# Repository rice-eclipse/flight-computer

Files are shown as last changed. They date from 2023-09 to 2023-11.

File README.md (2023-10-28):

# Strix
Custom STM32-Based flight computer to gather data from IMUs, altimeters, and GPS, and control in-flight pyrotechnic events. The software running on this board was created in STM32CubeMX, and stored in a different repository.

This repository contains KiCAD schematics and layouts for this flight computer. The schematics use hierarchical schematic sheets, with sheets defined for the microcontroller, sensors/data storage, pyrotechnic channels, connectors, and power supply.

## Notes
Manufacturing exports go in the fabrication folder (ignored by .gitignore)

## Additional Documentation:
[docs/strix.md](docs/strix.md)

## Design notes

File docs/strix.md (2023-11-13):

# Strix

Strix is a completely student researched and designed flight computer. It was created to record data, transmit telemetry, and control in-flight events in Eclipse's rockets. It is intended to supplement/replace altimeters and flight computers Eclipse currently uses, including the Missileworks RRC2+, Featherweight Altimeters Raven Blue, and Altus Metrum TeleMega.

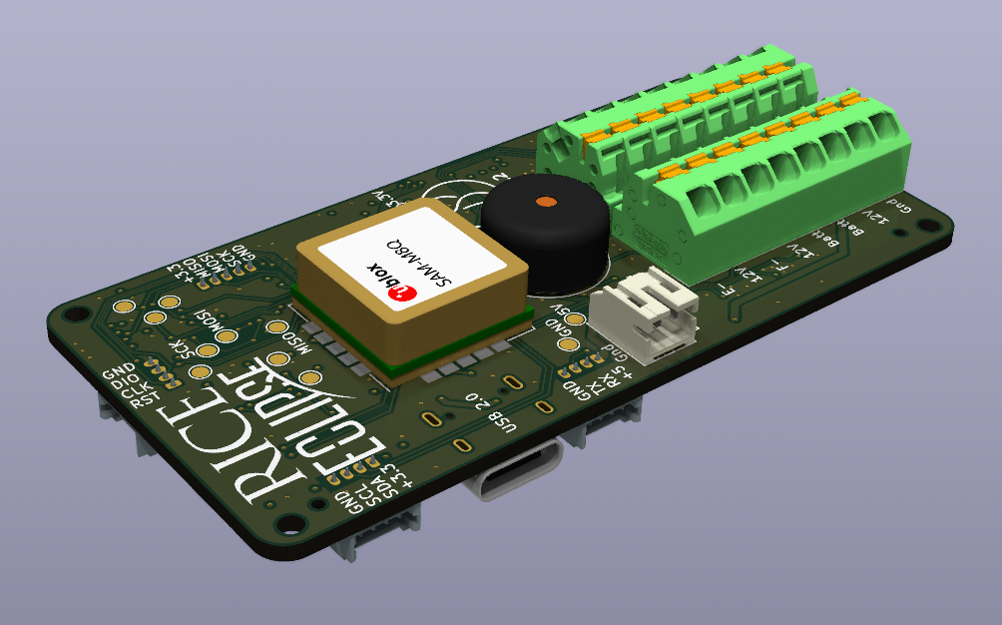
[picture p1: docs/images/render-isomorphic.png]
Isomorphic view of Strix


## Requirements

Strix was designed with several requirements in mind. It must:

1. Read linear and angular acceleration data from two different accelerometers
2. Read barometric altitude
3. Record data to flash memory and/or a MicroSD card
4. Perform sensor fusion to obtain an accurate estimate of a rocket's location
5. Control in-flight events using pyrotechnic charges and igniters

## Schematics

The design of Strix is split up into sections, each occupying a separate hierarchical sheet in the KiCAD project. These sections are the **Microcontroller, Pyrotechnic Charges, Sensors and Data Storage, Connectors, and Power Supply**.

### Microcontroller

### Pyrotechnic Charges

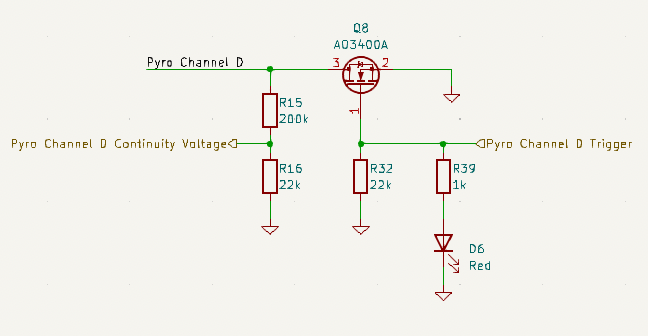
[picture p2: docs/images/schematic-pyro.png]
Pyrotechnic Charge schematic


Each pyrotechnic charge is actuated by an A03400A N-channel MOSFET. This is triggered by a GPIO output pin on the Microcontroller, along with an indicator LED to notify when a channel is active. The Pyrotechnic charge itself is attached to the +12V rail, representing the ignition battery positive voltage, and the - channel on the terminal block. This is then connected through a high impedance voltage divider to ground, to enable the microcontroller to read the voltage through this voltage divider and determine if there is continuity on the charge.

The terminal blocks for the pyrotechnic charges were chosen to provide an upgrade to the traiditionally used screw switches. Screw switches require using solid-core wire to avoid wires falling out due to vibrations in flight of the rocket, while terminal blocks like the Pheonix Contact 1861991 provide spring-loaded pressure that functions equally well with stranded core as well as solid core wire. Another reason these were chosen is the ease of swapping out wires into these lever nuts is another benefit of this choice.

### Sensors and Data Storage

The sensors used on this board are as follows:

- Bosch **BMI088** ruggedized accelerometer measuring $\pm$ 16 Gs
  - This is Bosch's accelerometer designed specifically for robotics and drone applications, and advertises high resistance to vibrations.
- Analog Devices **ADXL375** High-G accelerometer reading $\pm$ 64 Gs
- Bosch **BMP388** barometric pressure sensor
  - This was the second choice after the Measurement Specialties MS5611, but was chosen due to better stock at JLCPCB.
- U-blox **SAM-M10** GNSS receiver
  - This was chosen to provide a drop-in solution for GNSS reception, including an antenna. It increases cost by about $10 over alternatives without included antennas, but the decision was made to ensure GPS functionality.

### Connectors

The connectors were chosen to maximize ease of use and expandability. There are breakouts for external connections to dedicated SPI, I2C, and UART busses through Molex Picoblade connectors. A Molex Picoblade connector is also used for the Serial Wire Debug connection to the STM32 Microcontroller.

The connector schematic sheet contains the expansion ports, battery plug, and USB port, along with associated circuit elements. The USB port is a USB-C port running at USB 2.0 speeds, connected to a **USB-LC6** electrostatic discharge protection chip.

### Power Supply

<p float="center">
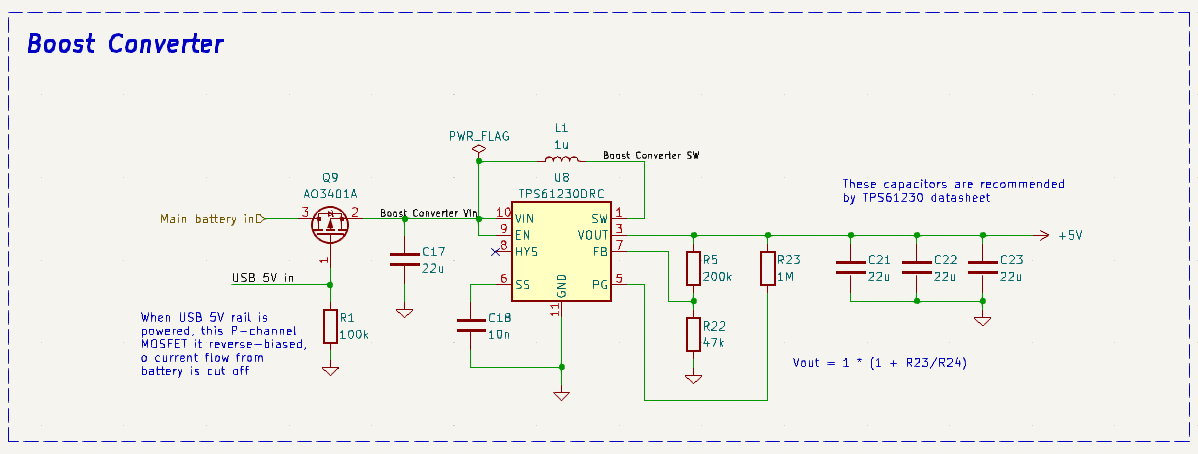
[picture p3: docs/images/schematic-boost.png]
Section of schematic showing boost converter
   
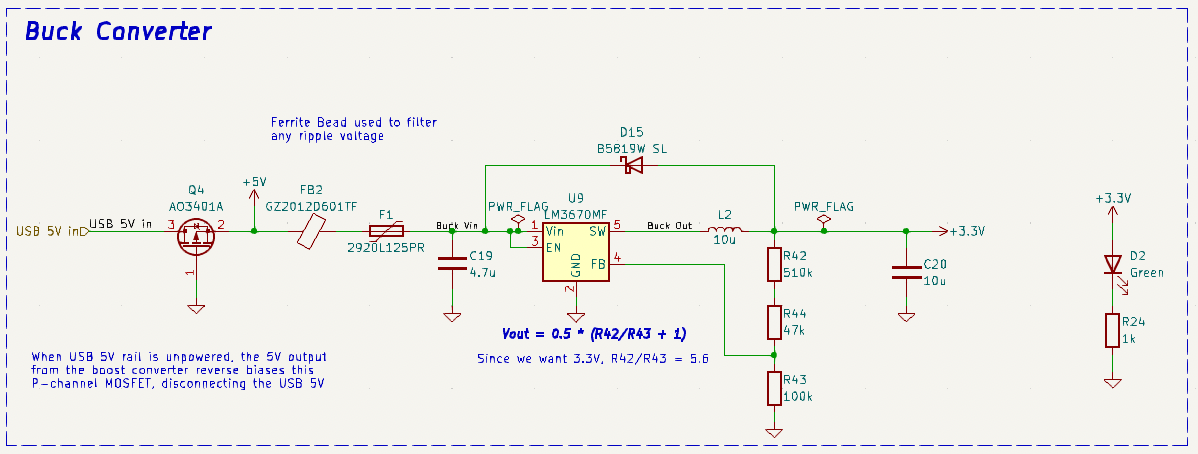
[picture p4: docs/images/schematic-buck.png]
Section of schematic showing buck converter
   
</div>

The power supply was designed to accept either USB bus voltage (between 4.5 and 5.5 volts) or battery voltage between 2 and 5 volts. This is acheived through a two phase boost-buck architecture. The boost converter, a **TPS61230**, first converts from the battery voltage to +5.1 volts, which is then combined with USB power and supplied to an **LM3670** buck converter to regulate down to +3.3 volts to supply the Microcontroller, sensors, flash storage chip, MicroSD card, and other assorted components.

To prioritize the USB input voltage over discharging a connected battery, the power supply makes use of a pair of P-channel MOSFETs, which also protect against reverse polarity battery connections. These are configured such that if the USB V<sub>bus</sub> rail is powered, the P-channel mosfet connected to the input of the boost converter is reverse-biased, so does not allow current to flow from the battery input. If the USB V<sub>bus</sub> is not powered, the gate of this MOSFET is connected to ground through a 100k Ohm resistor, which forward-biases the MOSFET and allows current to flow. The battery input is thus connected to the TPS61230, and the +5.1V output from this is connected to the LM3670, with a second P-channel MOSFET between this and the USB V<sub>bus</sub> rail. The gate of this second P-channel MOSFET is shorted to ground, which only allows current to flow from the V<sub>bus</sub> input to the LM3670, and not from the boost converter output back towards the USB connector. This is necessary to prevent the boost converter from turning itself off with its own output.

The surrounding components for both the Boost and Buck converter were chosen according to guidelines in the datasheets for both components.

## Layout

<p float="center">
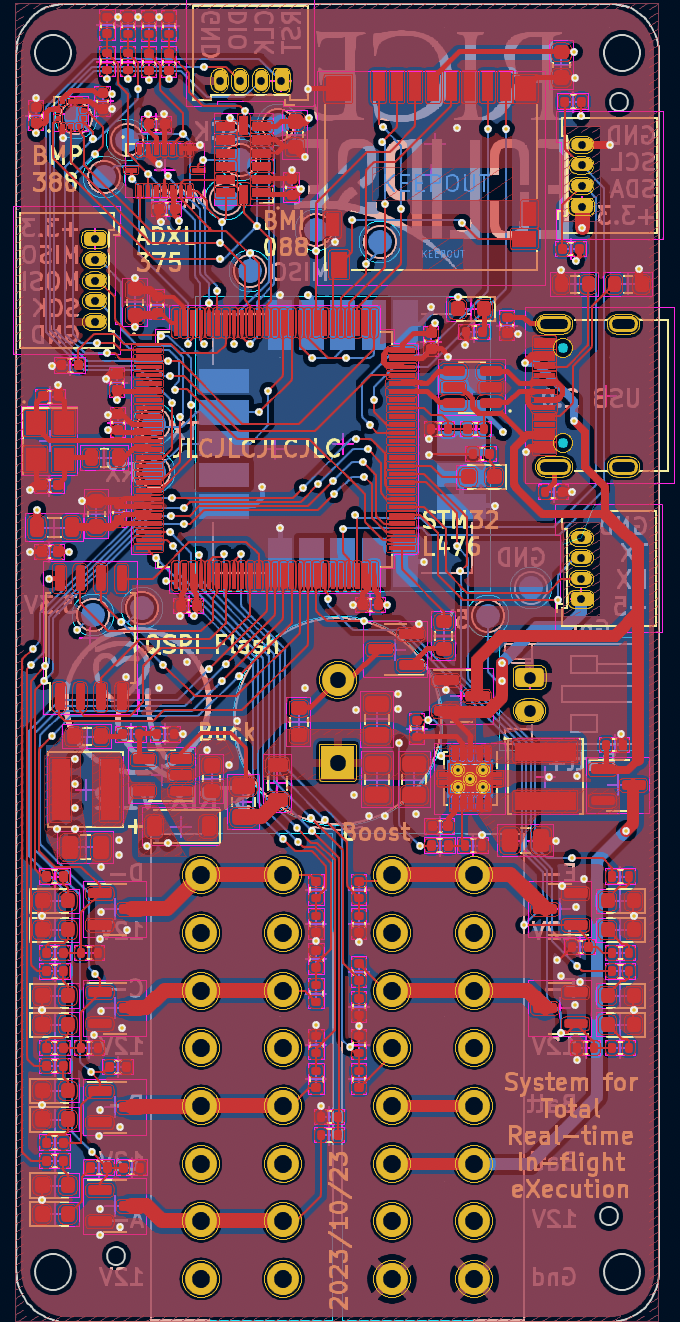
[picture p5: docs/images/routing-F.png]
Front Copper Pours and Traces

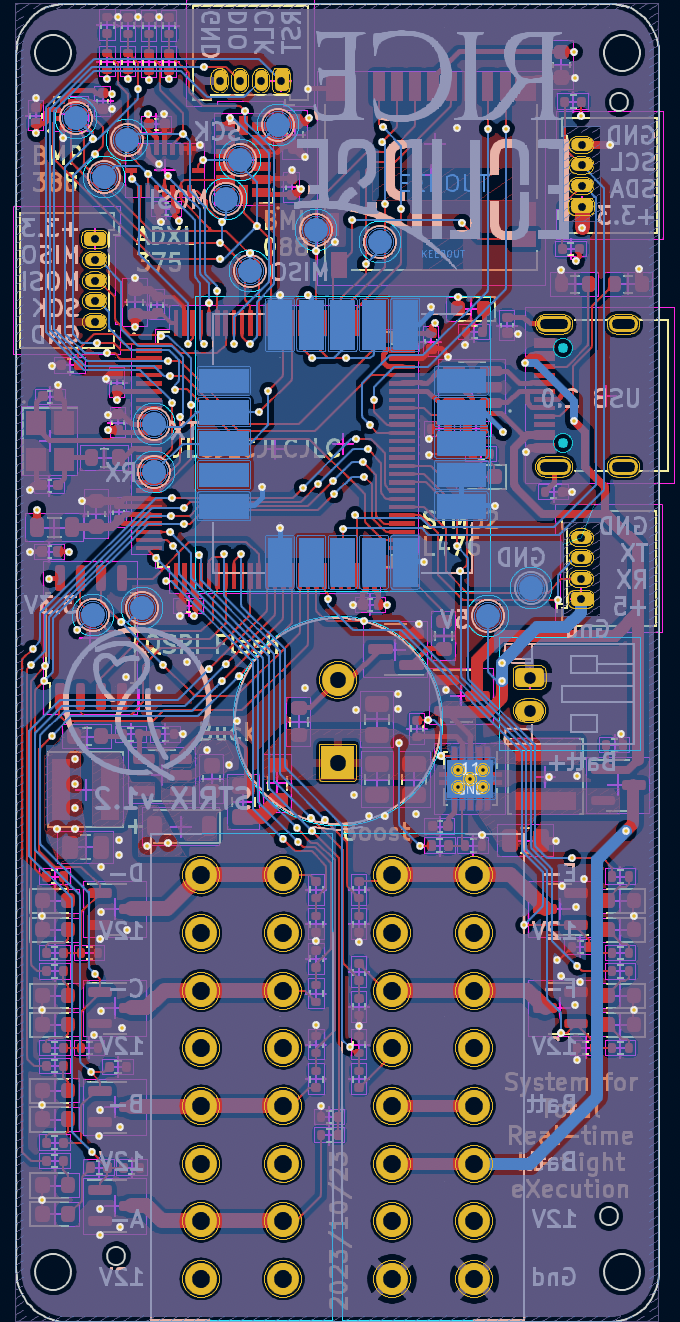
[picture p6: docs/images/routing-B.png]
Back Copper Pours and Traces

</p>

The layout was designed to optimize space consumption, as well as to facilitate ease-of-use and configurability. The expansion SPI, I2C, and UART ports are brought out to the edges of the board, as well as the serial wire debug port. Components are placed on both sides of the board, however all SMD components that can be assembled by JLSBCB are on the back (technically the F.Cu layer in KiCAD). The components left for the front are the Buzzer, GPS module, Main battery JST-PH plug, and terminal blocks for screw switches and Pyrotechnic charges.

### Physical Size

<p float="center">
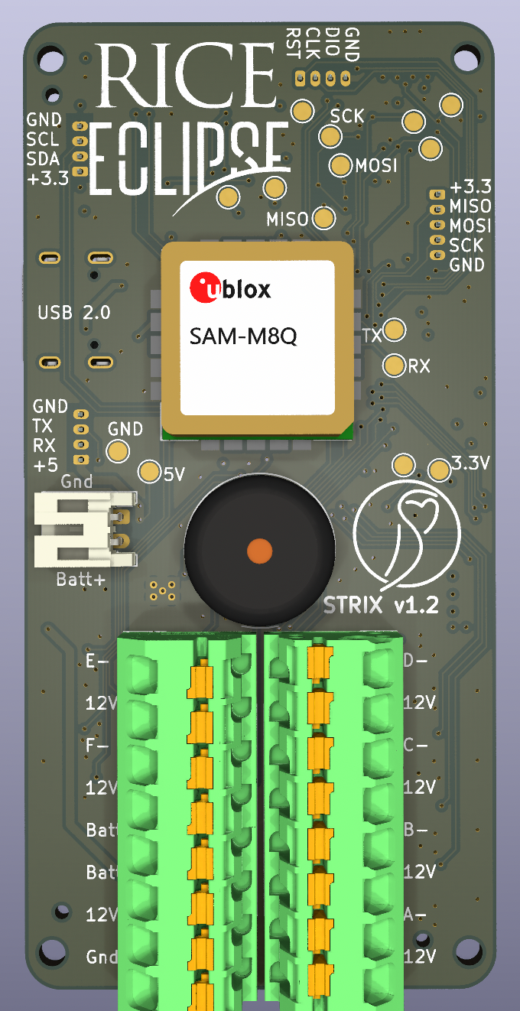
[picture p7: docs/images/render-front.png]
Render of front of board

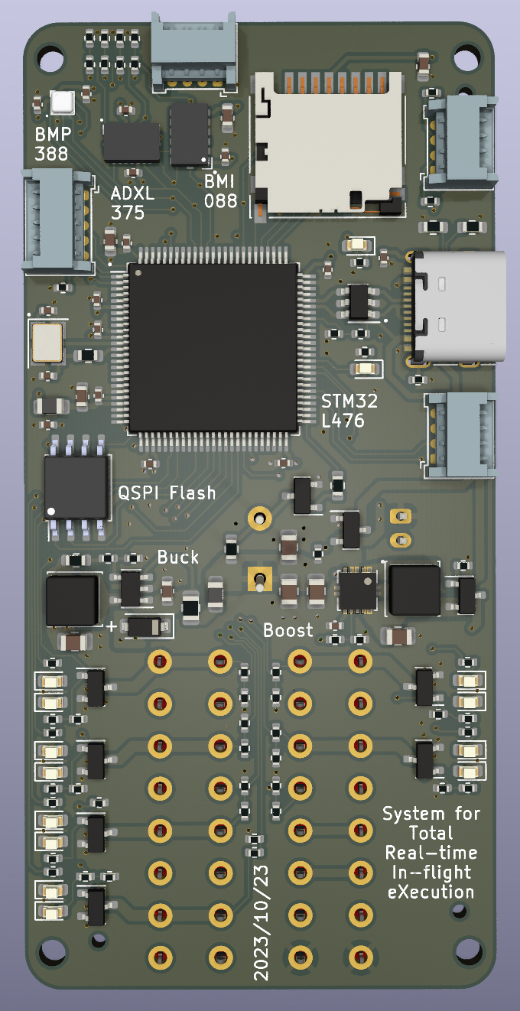
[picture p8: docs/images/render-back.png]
Render of back of board

</p>

The physical specifications of the board are: PCB 39mm wide by 80mm long. Components extend <3.5mm from the back, and up to 8mm from the front. Mounting holes are uniform distances from the edge of the PCB, and are spaced 33mm x 72mm apart on each corner.

### Test Point Locations

The test points are shown in the diagram below, and labeled in the following table:

Close up of test points on the B.Cu layer

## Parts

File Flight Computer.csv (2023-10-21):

Comment | Designator | Footprint | LCSC
Buzzer | BZ1 | Buzzer_Beeper:Buzzer_TDK_PS1240P02BT_D12.2mm_H6.5mm
1u | C1,C24 | Capacitor_SMD:C_0603_1608Metric
22u | C17,C21,C22,C23 | Capacitor_SMD:C_0805_2012Metric
10n | C18 | Capacitor_SMD:C_0402_1005Metric
4.7u | C19 | Capacitor_SMD:C_0603_1608Metric
100n | C2,C3,C4,C5,C8,C9,C11,C12,C13,C14,C15,C16,C29 | Capacitor_SMD:C_0402_1005Metric
10u | C20 | Capacitor_SMD:C_0805_2012Metric
4u7 | C7,C28 | Capacitor_SMD:C_0603_1608Metric
12p | C6,C10 | Capacitor_SMD:C_0402_1005Metric
B5819W SL | D15 | Diode_SMD:D_SOD-123
LED | D1,D2 | LED_SMD:LED_0603_1608Metric
LED | D3,D4,D5,D6,D7,D8 | LED_SMD:LED_0603_1608Metric_Pad1.05x0.95mm_HandSolder
2920L125PR | F1 | Fuse:Fuse_0805_2012Metric
GZ2012D601TF | FB1,FB2 | Inductor_SMD:L_0805_2012Metric
MountingHole | H1,H2,H3,H4 | MountingHole:MountingHole_2mm
Screw Switches | J1 | custom-footprints:Wago_Custom_218-108
Micro_SD_Card | J10 | Connector_Card:microSD_HC_Hirose_DM3D-SF
Pyro Channels | J2 | custom-footprints:Wago_Custom_218-108
Serial Wire Debug | J3 | Connector_PinHeader_2.54mm:PinHeader_2x02_P2.54mm_Vertical
JST-PH | J4 | Connector_JST:JST_PH_B2B-PH-K_1x02_P2.00mm_Vertical
USB_C_Receptacle_USB2.0 | J7 | Connector_USB:USB_C_Receptacle_G-Switch_GT-USB-7010ASV
External UART | J8 | Connector_Molex:Molex_PicoBlade_53048-0410_1x04_P1.25mm_Horizontal
External I2C | J9 | Connector_Molex:Molex_PicoBlade_53048-0410_1x04_P1.25mm_Horizontal
1u | L1 | Inductor_SMD:L_Sunlord_SWPA4030S
10u | L2 | Inductor_SMD:L_Sunlord_SWPA4030S
MMBT2222A | Q1 | Package_TO_SOT_SMD:SOT-23
AO3400A | Q2,Q3,Q5,Q6,Q7,Q8 | Package_TO_SOT_SMD:SOT-23
AO3401A | Q4,Q9 | Package_TO_SOT_SMD:SOT-23
100k | R1 | Resistor_SMD:R_0402_1005Metric
1k | R18,R28 | Resistor_SMD:R_0603_1608Metric
47 | R2 | Resistor_SMD:R_0603_1608Metric
5.1k | R20,R21 | Resistor_SMD:R_0603_1608Metric
47k | R22 | Resistor_SMD:R_0402_1005Metric
1M | R19,R23 | Resistor_SMD:R_0402_1005Metric
1.5k | R17,R24,R36,R37,R38,R39,R40,R41 | Resistor_SMD:R_0402_1005Metric
4.7k | R26,R27 | Resistor_SMD:R_0402_1005Metric
10k | R3 | Resistor_SMD:R_0402_1005Metric
200k | R4,R5,R7,R9,R11,R13,R15,R25 | Resistor_SMD:R_0402_1005Metric
22k | R6,R8,R10,R12,R14,R16,R29,R30,R31,R32,R33,R34,R35 | Resistor_SMD:R_0402_1005Metric
5V | TP1 | TestPoint:TestPoint_Pad_D1.5mm
UART2 TX | TP10 | TestPoint:TestPoint_Pad_D1.5mm
UART2 RX | TP11 | TestPoint:TestPoint_Pad_D1.5mm
Gnd | TP12 | TestPoint:TestPoint_Pad_D1.5mm
SDMMC Clock | TP13 | TestPoint:TestPoint_Pad_D1.5mm
SDMMC Command | TP14 | TestPoint:TestPoint_Pad_D1.5mm
QSPI Clock | TP15 | TestPoint:TestPoint_Pad_D1.5mm
3.3V | TP2 | TestPoint:TestPoint_Pad_D1.5mm
SPI1 MISO | TP3 | TestPoint:TestPoint_Pad_D1.5mm
SPI1 MOSI | TP4 | TestPoint:TestPoint_Pad_D1.5mm
SPI1 SCK | TP5 | TestPoint:TestPoint_Pad_D1.5mm
CS Altimeter | TP6 | TestPoint:TestPoint_Pad_D1.5mm
CS High G | TP7 | TestPoint:TestPoint_Pad_D1.5mm
CS Low G Gyro | TP8 | TestPoint:TestPoint_Pad_D1.5mm
CS Low G Accel | TP9 | TestPoint:TestPoint_Pad_D1.5mm
STM32L476VETx | U1 | Package_QFP:LQFP-100_14x14mm_P0.5mm
SAM-M8Q | U11 | RF_GPS:ublox_SAM-M8Q_HandSolder
USBLC6-2SC6 | U2 | Package_TO_SOT_SMD:SOT-23-6
~ | U3 | custom-footprints:ADXL375
~ | U4 | custom-footprints:BMI088
~ | U5 | custom-footprints:BMP388
W25Q128JVSIQ | U7 | Package_SO:SOIC-8_5.23x5.23mm_P1.27mm
TPS61230DRC | U8 | Package_SON:Texas_S-PVSON-N10_ThermalVias
LM3670MF | U9 | Package_TO_SOT_SMD:TSOT-23-5
16MHz | Y1 | Crystal:Crystal_SMD_3225-4Pin_3.2x2.5mm

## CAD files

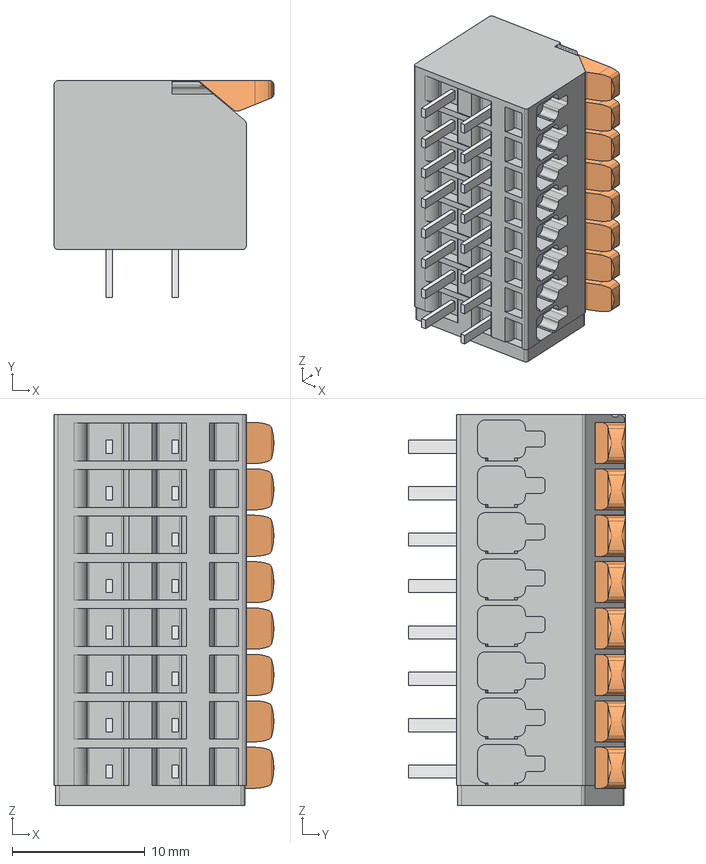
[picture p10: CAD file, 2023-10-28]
models/2601-1108.stp
16.6 x 16.4 x 29.5 mm

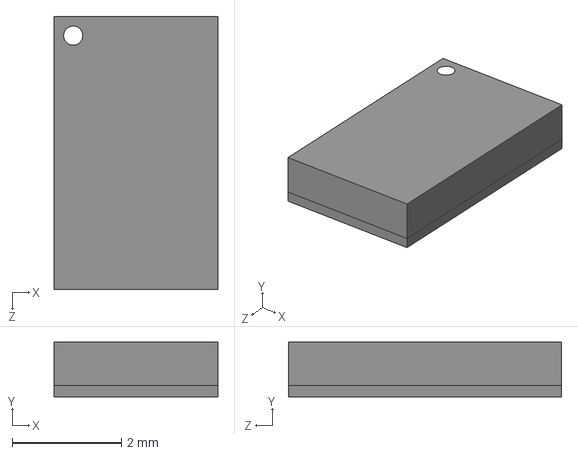
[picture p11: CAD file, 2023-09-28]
models/ADXL375BCCZ-RL7.STEP
3.00 x 1.00 x 5.00 mm

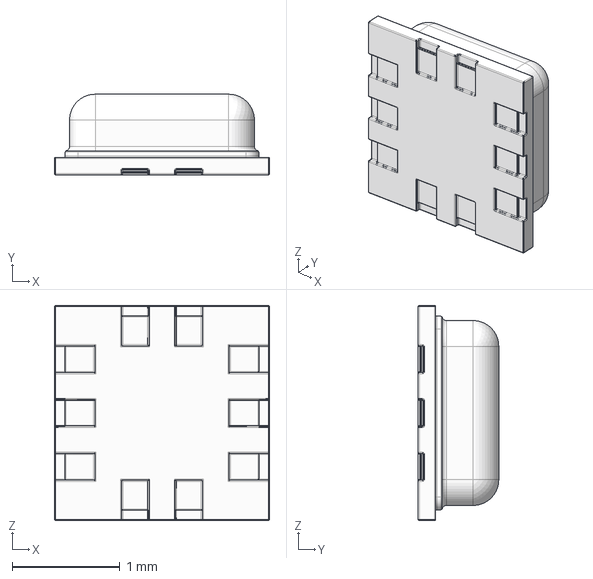
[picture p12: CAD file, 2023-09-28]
models/Bosch BMP388.step
2.00 x 0.75 x 2.00 mm

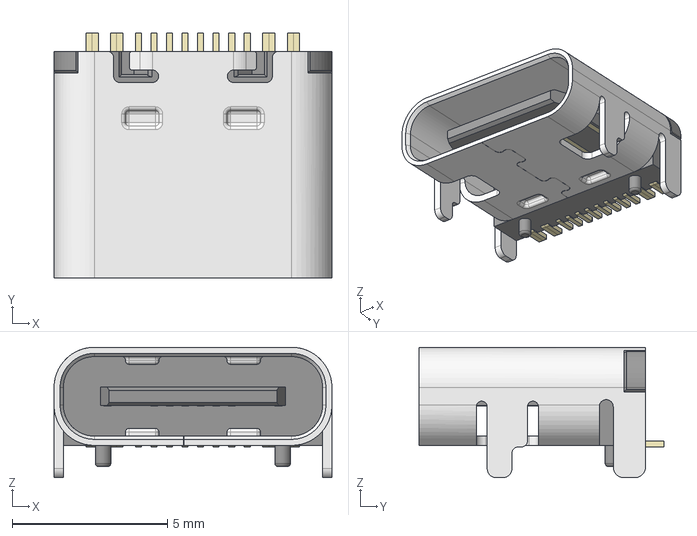
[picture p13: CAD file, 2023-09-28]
models/HRO_TYPE-C-31-M-12.step
8.95 x 7.90 x 4.20 mm

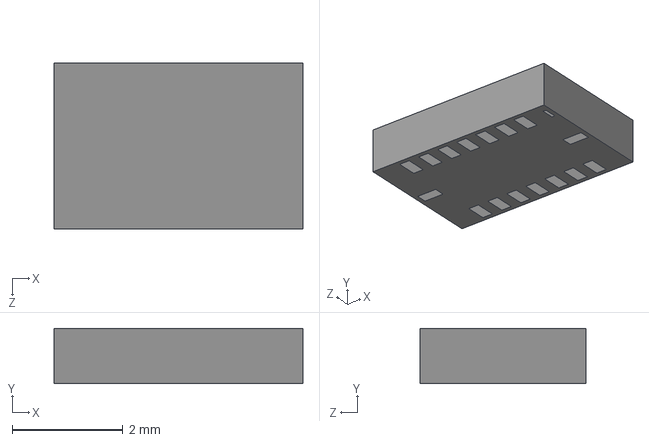
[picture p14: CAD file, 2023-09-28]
models/BMI088--3DModel-STEP-56544.STEP
4.50 x 1.00 x 3.00 mm

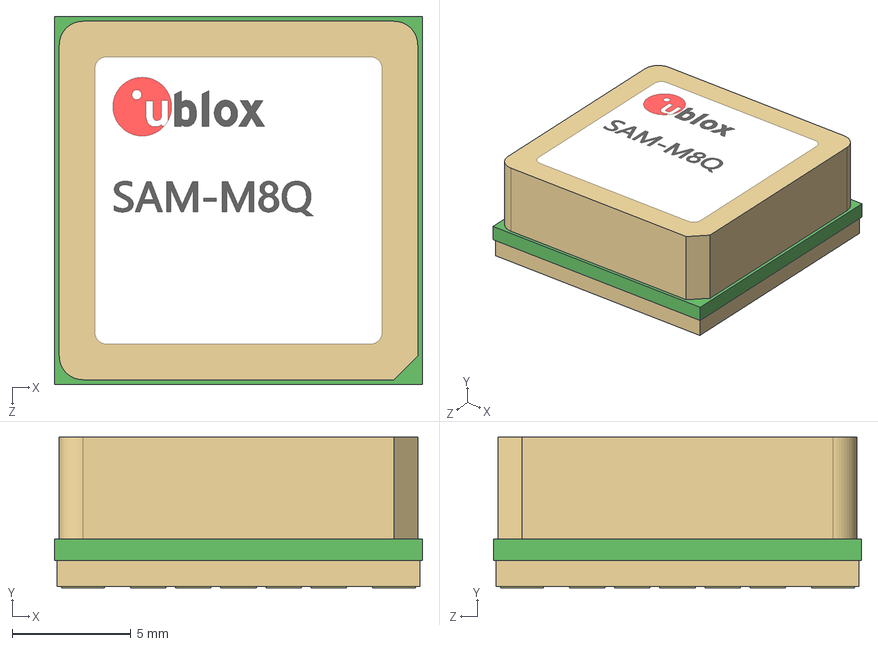
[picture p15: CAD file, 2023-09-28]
models/GPS_sam-m8q.STEP
15.5 x 6.35 x 15.5 mm

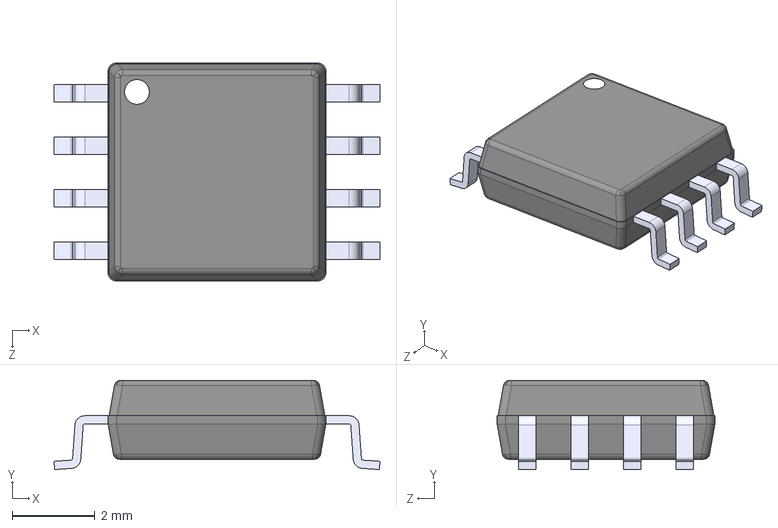
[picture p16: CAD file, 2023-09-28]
models/W25Q128JVSIQ.STEP
7.90 x 2.16 x 5.28 mm

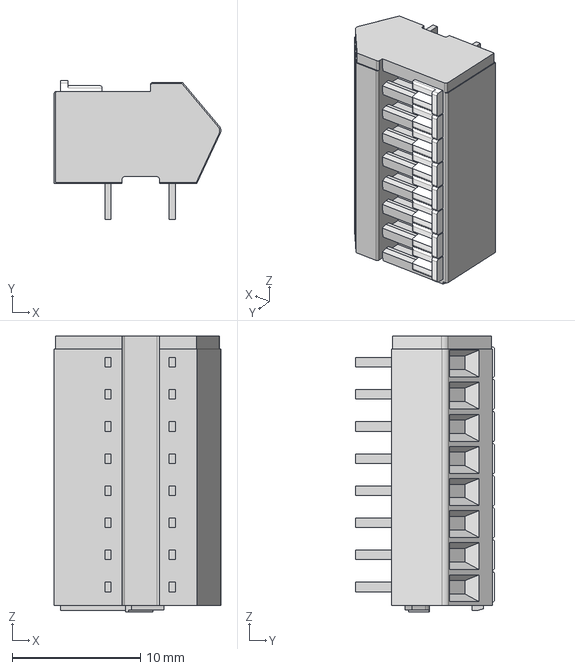
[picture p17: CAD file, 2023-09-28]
models/218-108.stp
13.0 x 10.9 x 21.5 mm

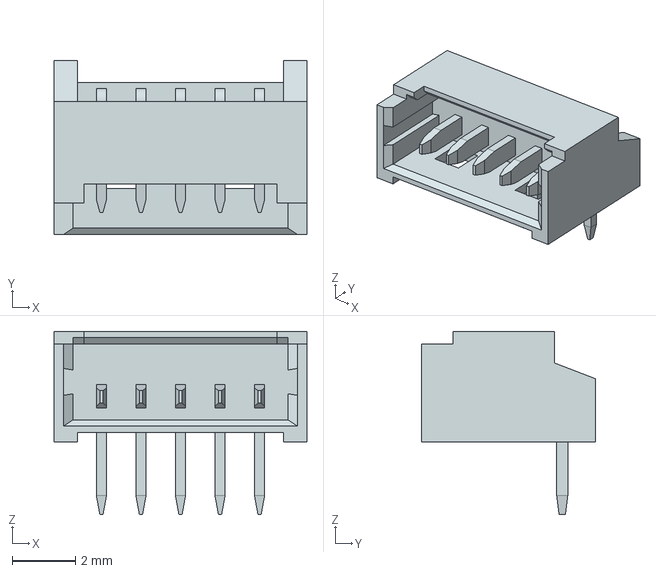
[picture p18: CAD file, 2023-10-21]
models/530480510.stp
8.00 x 5.50 x 5.80 mm

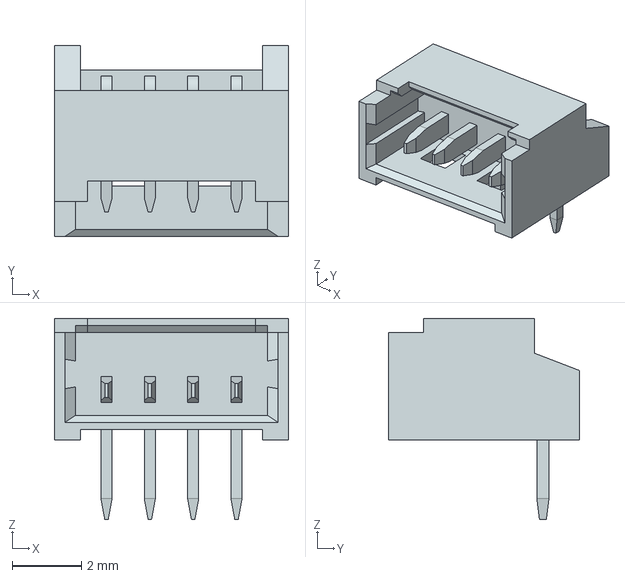
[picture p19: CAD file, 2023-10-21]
models/530480410.stp
6.75 x 5.50 x 5.80 mm

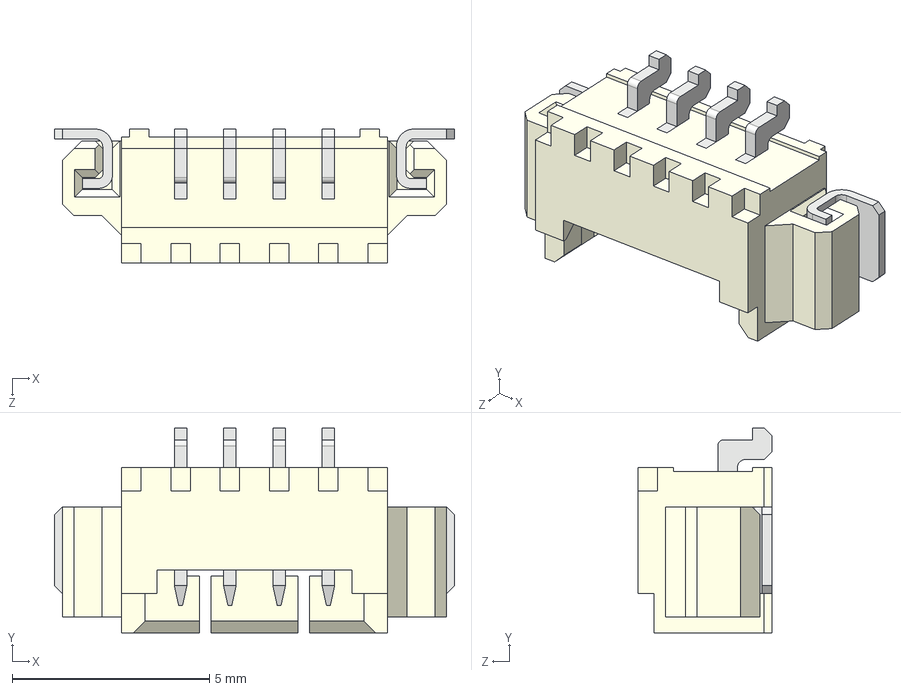
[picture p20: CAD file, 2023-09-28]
models/532610471.STEP
10.1 x 5.20 x 3.40 mm

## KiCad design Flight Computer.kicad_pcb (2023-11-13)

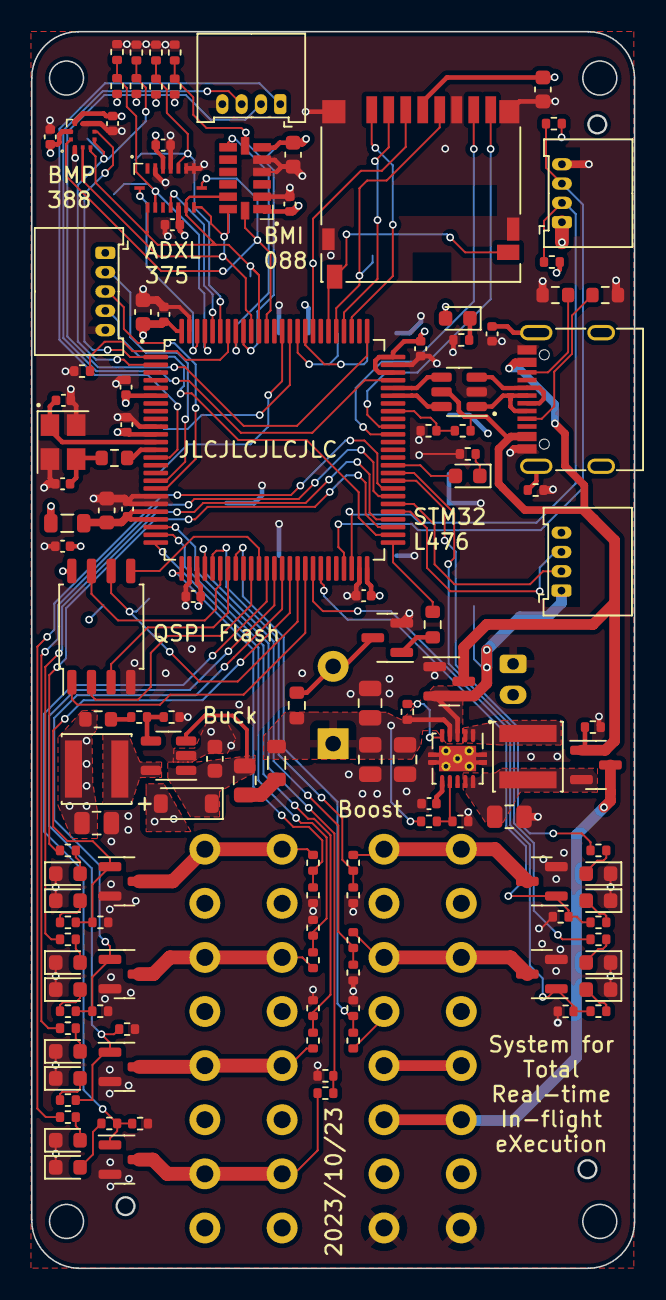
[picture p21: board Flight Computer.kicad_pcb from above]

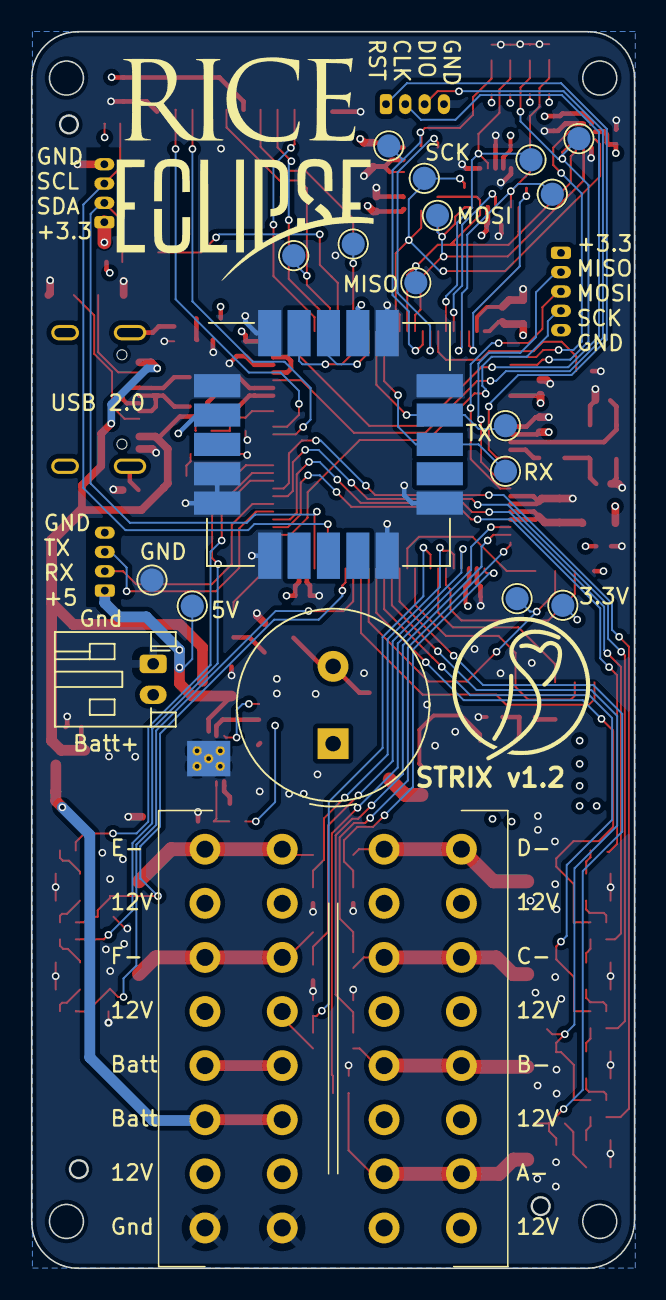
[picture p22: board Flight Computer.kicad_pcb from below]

Board: 4 copper layers, 39.0 x 80.0 mm, 151 parts (20 on the bottom side), 111 nets.

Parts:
BZ1: Buzzer; Buzzer_TDK_PS1240P02BT_D12.2mm_H6.5mm
C1, C24: 1u; C_0603_1608Metric
C2, C3, C4, C5, C8, C9, C11, C12, C13, C14, C15, C16, C29: 100n; C_0402_1005Metric
C6, C10: 12p; C_0402_1005Metric
C7, C28: 4u7; C_0603_1608Metric
C17, C21, C22, C23: 22u; C_0805_2012Metric
C18: 10n; C_0402_1005Metric
C19: 4.7u; C_0603_1608Metric
C20: 10u; C_0805_2012Metric
C25: 0.01u; C_0402_1005Metric
D1: Blue; LED_0603_1608Metric
D2: Green; LED_0603_1608Metric
D3, D4, D5, D6, D7, D8: Red; LED_0603_1608Metric
D9, D10, D11, D12, D13, D14: White; LED_0603_1608Metric
D15: B5819W SL; D_SOD-123
F1: 2920L125PR; Fuse_0805_2012Metric
FB1, FB2: GZ2012D601TF; L_0805_2012Metric
J1: Screw Switches; Pheonix-Contact-1861991
J2: Pyro Channels; Pheonix-Contact-1861991
J4: JST-PH; JST_PH_S2B-PH-K_1x02_P2.00mm_Horizontal
J5: External SPI; Molex_PicoBlade_53048-0510_1x05_P1.25mm_Horizontal
J6: Serial Wire Debug; Molex_PicoBlade_53048-0410_1x04_P1.25mm_Horizontal
J7: USB_C_Receptacle_USB2.0; USB_C_Receptacle_G-Switch_GT-USB-7010ASV
J8: External UART; Molex_PicoBlade_53048-0410_1x04_P1.25mm_Horizontal
J9: External I2C; Molex_PicoBlade_53048-0410_1x04_P1.25mm_Horizontal
J10: Micro_SD_Card; microSD_HC_Hirose_DM3D-SF
L1: 1u; L_Sunlord_SWPA4030S
L2: 10u; L_Sunlord_SWPA4030S
Q1: MMBT2222A; SOT-23
Q2, Q3, Q5, Q6, Q7, Q8: AO3400A; SOT-23
Q4, Q9: AO3401A; SOT-23
R1, R43: 100k; R_0402_1005Metric
R2: 47; R_0603_1608Metric
R3: 10k; R_0402_1005Metric
R4, R5, R7, R9, R11, R13, R15, R25, R46: 200k; R_0402_1005Metric
R6, R8, R10, R12, R14, R16, R29, R30, R31, R32, R33, R34, R35: 22k; R_0402_1005Metric
R17, R24, R36, R37, R38, R39, R40, R41, R47, R56, R57, R58, R59, R60: 1k; R_0402_1005Metric
R18, R28: 1k; R_0603_1608Metric
R19, R23: 1M; R_0402_1005Metric
R20, R21: 5.1k; R_0603_1608Metric
R22, R44, R45: 47k; R_0402_1005Metric
R26, R27: 4.7k; R_0402_1005Metric
R42: 510k; R_0603_1608Metric
R48, R49, R50, R51, R52, R53, R54, R55: 0; R_0402_1005Metric
TP1: 5V; TestPoint_Pad_D1.5mm
TP2: 3.3V; TestPoint_Pad_D1.5mm
TP3: SPI1 MISO; TestPoint_Pad_D1.5mm
TP4: SPI1 MOSI; TestPoint_Pad_D1.5mm
TP5: SPI1 SCK; TestPoint_Pad_D1.5mm
TP6: CS Altimeter; TestPoint_Pad_D1.5mm
TP7: CS High G; TestPoint_Pad_D1.5mm
TP8: CS Low G Gyro; TestPoint_Pad_D1.5mm
TP9: CS Low G Accel; TestPoint_Pad_D1.5mm
TP10: UART2 TX; TestPoint_Pad_D1.5mm
TP11: UART2 RX; TestPoint_Pad_D1.5mm
TP12: Gnd; TestPoint_Pad_D1.5mm
TP13: SDMMC Clock; TestPoint_Pad_D1.5mm
TP14: SDMMC Command; TestPoint_Pad_D1.5mm
TP15: QSPI Clock; TestPoint_Pad_D1.5mm
U1: STM32L476VETx; LQFP-100_14x14mm_P0.5mm
U2: USBLC6-2SC6; SOT-23-6
U3: ADXL375
U4: BMI088
U5: BMP388
U7: W25Q128JVSIQ; SOIC-8_5.23x5.23mm_P1.27mm
U8: TPS61230DRC; Texas_S-PVSON-N10_ThermalVias
U9: LM3670MF; TSOT-23-5
U11: SAM-M8Q; ublox_SAM-M8Q_HandSolder
Y1: 16MHz; Crystal_SMD_3225-4Pin_3.2x2.5mm

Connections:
+3.3V: C1.1, C2.1, C3.1, C4.1, C5.1, C7.1, C8.1, C9.1, C11.1, C12.1, C13.1, C14.1, C15.1, C20.1, C28.1, C29.1, D2.2 (A), D15.2 (A), FB1.2, J5.1, J9.1, J10.4 (VDD), L2.2, R26.1, R27.1, R42.1, R48.1, R50.1, R52.1, R54.1, TP2.1, U1.6 (VBAT), U1.11 (VDD), U1.28 (VDD), U1.50 (VDD), U1.73 (VDDUSB), U1.75 (VDD), U1.100 (VDD), U3.1 (Vdd), U3.6 (Vs), U4.3 (Vdd), U4.11 (Vddio), U5.1 (Vddio), U5.10 (Vdd), U7.8 (VCC), U11.2 (VCC_IO), U11.17 (VCC)
+5V: BZ1.1 (-), C21.1, C22.1, C23.1, FB2.1, J8.1, Q4.2 (S), R5.1, R23.1, R28.1, TP1.1, U8.3 (VOUT), U8.4 (VOUT)
+12V: J1.3, J1.4, J1.7, J1.8, J1.13, J1.14, J2.1, J2.2, J2.5, J2.6, J2.9, J2.10, J2.13, J2.14, R25.1
/Altimeter Interrupt: U1.1 (PE2), U5.7 (Interrupt)
/Chip Select Altimeter: R54.2, R55.1, TP6.1, U1.2 (PE3), U5.6 (Chip_Select)
/Chip Select High G Accel: R48.2, R49.1, TP7.1, U1.92 (PB6), U3.7 (Chip_Select)
/Chip Select Low G Accel: R50.2, R51.1, TP8.1, U1.97 (PE0), U4.14 (Chip_Select_Accel)
/Chip Select Low G Gyro: R52.2, R53.1, TP9.1, U1.95 (PB8), U4.5 (Chip_Select_Gyro)
/Connectors and Power Supply/Power Supply/Boost Converter SW: L1.2, U8.1 (SW), U8.2 (SW)
/Connectors and Power Supply/Power Supply/Boost Converter Vin: C17.1, L1.1, Q9.2 (S), U8.9 (EN), U8.10 (VIN)
/Connectors and Power Supply/Power Supply/Buck Out: L2.1, U9.5 (SW)
/Connectors and Power Supply/Power Supply/Buck Vin: C19.1, D15.1 (K), F1.2, U9.1 (Vin), U9.3 (EN)
/Connectors and Power Supply/USB CONN D+: J7.A6 (D+), J7.B6 (D+), U2.3 (I/O2)
/Connectors and Power Supply/USB CONN D-: J7.A7 (D-), J7.B7 (D-), U2.1 (I/O1)
/GPS External Interrupt: U1.84 (PD3), U11.19 (EXTINT)
/GPS Reset: U1.85 (PD4), U11.18 (~RESET)
/High G Interrupt: U1.93 (PB7), U3.8 (Interrupt_1)
/I2C2 SCL: J9.3, R26.2, U1.47 (PB10)
/I2C2 SDA: J9.2, R27.2, U1.48 (PB11)
/Ignition Battery Voltage: R25.2, R35.1, U1.33 (PC4)
/Low G Accel Interrupt: U1.98 (PE1), U4.16 (Interrupt_1)
/Low G Gyro Interrupt: U1.96 (PB9), U4.12 (Interrupt_3)
/Main battery connector: J1.9, J1.10, J4.2
/Main battery in: J1.11, J1.12, Q9.3 (D)
/Microcontroller/VDDA: C16.1, C24.1, FB1.1, U1.21 (VREF+), U1.22 (VDDA)
/NRST: J6.1, U1.14 (NRST)
/Pyro A Continuity LED: R47.1, U1.58 (PD11)
/Pyro A Continuity Voltage: R4.2, R6.1, U1.23 (PA0)
/Pyro B Continuity LED: R56.1, U1.57 (PD10)
/Pyro B Continuity Voltage: R7.2, R8.1, U1.24 (PA1)
/Pyro C Continuity LED: R57.1, U1.54 (PB15)
/Pyro C Continuity Voltage: R9.2, R10.1, U1.25 (PA2)
/Pyro Channel A Trigger: Q2.1 (G), R34.1, R36.1, U1.37 (PB2)
/Pyro Channel B Trigger: Q3.1 (G), R29.1, R40.1, U1.38 (PE7)
/Pyro Channel C Trigger: Q5.1 (G), R33.1, R41.1, U1.39 (PE8)
/Pyro Channel D Trigger: Q8.1 (G), R32.1, R39.1, U1.40 (PE9)
/Pyro Channel E Trigger: Q6.1 (G), R30.1, R37.1, U1.44 (PE13)
/Pyro Channel F Trigger: Q7.1 (G), R31.1, R38.1, U1.43 (PE12)
/Pyro D Continuity LED: R58.1, U1.53 (PB14)
/Pyro D Continuity Voltage: R15.2, R16.1, U1.26 (PA3)
/Pyro E Continuity LED: R59.1, U1.59 (PD12)
/Pyro E Continuity Voltage: R11.2, R12.1, U1.30 (PA5)
/Pyro F Continuity LED: R60.1, U1.60 (PD13)
/Pyro F Continuity Voltage: R13.2, R14.1, U1.29 (PA4)
/Pyrotechnic Channels/Pyro Channel A: J2.3, J2.4, Q2.3 (D), R4.1
/Pyrotechnic Channels/Pyro Channel B: J2.7, J2.8, Q3.3 (D), R7.1
/Pyrotechnic Channels/Pyro Channel C: J2.11, J2.12, Q5.3 (D), R9.1
/Pyrotechnic Channels/Pyro Channel D: J2.15, J2.16, Q8.3 (D), R15.1
/Pyrotechnic Channels/Pyro Channel E: J1.1, J1.2, Q6.3 (D), R11.1
/Pyrotechnic Channels/Pyro Channel F: J1.5, J1.6, Q7.3 (D), R13.1
/QSPI Chip Select: U1.42 (PE11), U7.1 (~CS)
/QSPI Clock: TP15.1, U1.41 (PE10), U7.6 (CLK)
/QSPI IO0: U1.36 (PB1), U7.5 (DI(IO0))
/QSPI IO1: U1.35 (PB0), U7.2 (DO(IO1))
/QSPI IO2: U1.32 (PA7), U7.3 (IO2)
/QSPI IO3: U1.31 (PA6), U7.7 (IO3)
/SD Card Detect: J10.9 (DET_B), J10.10 (DET_A), U1.81 (PD0)
/SDMMC Clock: J10.5 (CLK), TP13.1, U1.80 (PC12)
/SDMMC Command: J10.3 (CMD), TP14.1, U1.83 (PD2)
/SDMMC Data 0: J10.7 (DAT0), U1.65 (PC8)
/SDMMC Data 1: J10.8 (DAT1), U1.66 (PC9)
/SDMMC Data 2: J10.1 (DAT2), U1.78 (PC10)
/SDMMC Data 3: J10.2 (DAT3/CD), U1.79 (PC11)
/SPI1 MISO: TP3.1, U1.90 (PB4), U3.12 (SDO/Addr_sel), U4.10 (SDO2), U4.15 (SDO1), U5.5 (SDO)
/SPI1 MOSI: TP4.1, U1.91 (PB5), U3.13 (SDA/SDI), U4.9 (SDA/SDI), U5.4 (SDI)
/SPI1 SCK: TP5.1, U1.89 (PB3), U3.14 (SCL/SCK), U4.8 (SCL/SCK), U5.2 (SCK)
/SPI2 MISO: J5.2, U1.17 (PC2)
/SPI2 MOSI: J5.3, U1.18 (PC3)
/SPI2 SCK: J5.4, U1.52 (PB13)
/SWCLK: J6.2, U1.76 (PA14)
/SWDIO: J6.3, U1.72 (PA13)
/UART2 RX: TP11.1, U1.87 (PD6), U11.13 (TXD)
/UART2 TX: TP10.1, U1.86 (PD5), U11.14 (RXD)
/UART3 RX: J8.2, U1.56 (PD9)
/UART3 TX: J8.3, U1.55 (PD8)
/USB 5V in: J7.A4 (VBUS), J7.A9 (VBUS), J7.B4 (VBUS), J7.B9 (VBUS), Q4.3 (D), Q9.1 (G), R1.1, R45.1, U2.5 (VBUS)
/USB D+: U1.71 (PA12), U2.4 (I/O2)
/USB D-: U1.70 (PA11), U2.6 (I/O1)
GND: C1.2, C2.2, C3.2, C4.2, C5.2, C6.2, C7.2, C8.2, C9.2, C10.2, C11.2, C12.2, C13.2, C14.2, C15.2, C16.2, C17.2, C18.2, C19.2, C20.2, C21.2, C22.2, C23.2, C24.2, C25.2, C28.2, C29.2, D3.1 (K), D4.1 (K), D5.1 (K), D6.1 (K), D7.1 (K), D8.1 (K), D9.1 (K), D10.1 (K), D11.1 (K), D12.1 (K), D13.1 (K), D14.1 (K), J1.15, J1.16, J4.1, J5.5, J6.4, J7.A1 (GND), J7.A12 (GND), J7.B1 (GND), J7.B12 (GND), J8.4, J9.4, J10.6 (VSS), J10.11 (SHIELD), Q1.2 (E), Q2.2 (S), Q3.2 (S), Q4.1 (G), Q5.2 (S), Q6.2 (S), Q7.2 (S), Q8.2 (S), R1.2, R3.1, R6.2, R8.2, R10.2, R12.2, R14.2, R16.2, R17.2, R19.2, R20.2, R21.2, R22.2, R24.2, R29.2, R30.2, R31.2, R32.2, R33.2, R34.2, R35.2, R43.2, R46.2, R49.2, R51.2, R53.2, R55.2, TP12.1, U1.10 (VSS), U1.19 (VSSA), U1.20 (VREF-), U1.27 (VSS), U1.49 (VSS), U1.74 (VSS), U1.99 (VSS), U2.2 (GND), U3.2 (GND), U3.4 (GND), U3.5 (GND), U4.2 (NC), U4.4 (GNDA), U4.6 (GNDIO), U4.7 (Protocol_Select), U5.3 (GND), U5.8 (GND), U5.9 (GND), U7.4 (GND), U8.11 (GND), U9.2 (GND), U11.1 (GND), U11.4 (GND), U11.5 (GND), U11.6 (GND), U11.10 (GND), U11.11 (GND), U11.15 (GND), U11.16 (GND), U11.20 (GND), Y1.2, Y1.4
unnamed: BZ1.2 (+), Q1.3 (C), R28.2
unnamed: C10.1, R2.2, Y1.3
unnamed: D1.2 (A), U1.61 (PD14)
unnamed: D1.1 (K), R17.1
unnamed: D2.1 (K), R24.1
unnamed: D3.2 (A), R36.2
unnamed: D4.2 (A), R37.2
unnamed: D5.2 (A), R38.2
unnamed: D6.2 (A), R39.2
unnamed: D7.2 (A), R40.2
unnamed: D8.2 (A), R41.2
unnamed: D9.2 (A), R47.2
unnamed: D10.2 (A), R56.2
unnamed: D11.2 (A), R57.2
unnamed: D12.2 (A), R58.2
unnamed: D13.2 (A), R59.2
unnamed: D14.2 (A), R60.2
unnamed: F1.1, FB2.2
unnamed: J7.A5 (CC1), R20.1
unnamed: J7.B5 (CC2), R21.1
unnamed: C25.1, J7.S1 (SHIELD), R19.1
unnamed: Q1.1 (B), R18.2
unnamed: R42.2, R44.1
unnamed: R3.2, U1.94 (BOOT0)
unnamed: R45.2, R46.1, U1.68 (PA9)
unnamed: R18.1, U1.51 (PB12)
unnamed: C6.1, U1.12 (PH0), Y1.1
unnamed: R2.1, U1.13 (PH1)
unnamed: R5.2, R22.1, U8.7 (FB)
unnamed: R23.2, U8.5 (PG)
unnamed: C18.1, U8.6 (SS)
unnamed: R43.1, R44.2, U9.4 (FB)

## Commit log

2023-09-19 Added symbols for sensors and power supply
    [Flight Computer.kicad_pcb, Flight Computer.kicad_sch, connectors.kicad_sch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]
2023-09-20 Finished Updating Sensor Schematics
    [sensors.kicad_sch]
2023-09-23 Added power supply circuitry, as well as example pyrotechnic channel MOSFET
    [power-supply.kicad_sch, pyro-channels.kicad_sch]
2023-09-24 Schematics are love. Also I have no idea what I was doing last night so the power supply might be terrible, but I know I thought it was brilliant at the time
    [Flight Computer.kicad_sch, connectors.kicad_sch, pyro-channels.kicad_sch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]
2023-09-24 Began configuring STM32F476
    [Flight Computer.kicad_sch]
2023-09-25 add microsd + flash schematics
    [sensors.kicad_sch]
2023-09-25 173 Errors. I'm going to take a break
    [Flight Computer.kicad_sch, connectors.kicad_sch, pyro-channels.kicad_sch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]
2023-09-25 Fixed all correct errors
    [Flight Computer.kicad_sch, connectors.kicad_sch, sensors.kicad_sch]
2023-09-26 Chose footprints for most components
    [Flight Computer.kicad_sch, connectors.kicad_sch, pyro-channels.kicad_sch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]
2023-09-27 Added custom footprints and started layout
    [Flight Computer.kicad_pcb, Flight Computer.kicad_sch, connectors.kicad_sch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]
2023-09-27 Started footprint
    [Flight Computer.kicad_pcb, Flight Computer.kicad_sch, connectors.kicad_sch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]
2023-09-28 Made more progress on layout
    [Flight Computer.kicad_pcb, Flight Computer.kicad_sch, connectors.kicad_sch]
2023-09-28 I sure hope I come up with a better layout than this for the pyro channels
    [Flight Computer.kicad_pcb, Flight Computer.kicad_sch, connectors.kicad_sch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]
2023-09-28 Finished first draft of layout
    [218-108.stp, 532610471.STEP, ADXL375BCCZ-RL7.STEP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]
2023-09-29 How many sheets do you want? Yes
    [Flight Computer.kicad_sch, connectors.kicad_sch, microcontroller.kicad_sch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]
2023-09-29 Finished updating the schematics
    [Flight Computer.kicad_sch, microcontroller.kicad_sch, power-supply.kicad_sch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]
2023-09-30 Started doing layout for v1.1
    [Flight Computer.kicad_pcb, Flight Computer.kicad_sch, microcontroller.kicad_sch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]
2023-10-01 finished layout for v1.1
    [Flight Computer.kicad_pcb, connectors.kicad_sch, microcontroller.kicad_sch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]
2023-10-05 How many test points do you want? Yes.
    [Flight Computer.csv, Flight Computer.kicad_sch, power-supply.kicad_sch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]
2023-10-05 Now with 100% fewer faulty flyback diodes
    [Flight Computer.kicad_pcb, pyro-channels.kicad_sch]
2023-10-10 Updated BOM
    [Flight Computer.csv, Flight Computer.kicad_pcb]
2023-10-10 Updated to match JLC manufacturing capabilities
    [Flight Computer.kicad_pcb, microcontroller.kicad_sch, power-supply.kicad_sch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]
2023-10-11 More JLC stuff
    [Flight Computer.kicad_pcb]
2023-10-13 Updated with notes from Erik Welsh
    [Flight Computer.kicad_pcb, connectors.kicad_sch, microcontroller.kicad_sch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]
2023-10-14 KiCAD is broken
    [530480410.stp, Flight Computer.kicad_pcb]
2023-10-15 Fabrication outputs
    [Flight Computer-B_Cu.gbr, Flight Computer-B_Mask.gbr, Flight Computer-B_Paste.gbr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]
2023-10-18 Minore changes and updates
    [Flight Computer.kicad_pcb]
2023-10-19 Fixed battery polarity
    [Flight Computer.kicad_pcb, connectors.kicad_sch]
2023-10-19 Updating with notes from Adam
    [Flight Computer.kicad_pcb, Flight Computer.kicad_sch, connectors.kicad_sch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]
2023-10-21 Finished final(tm) updates for v1.1
    [Flight Computer.kicad_pcb, Flight Computer.kicad_sch, connectors.kicad_sch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]
2023-10-21 Added logo and 3D model for 5-pin picoblade
    [530480510.stp, Flight Computer.kicad_pcb]
2023-10-21 Started updating documentation
    [microcontroller 2.kicad_sch]
2023-10-22 Added old version of BOM
    [Flight Computer.csv]
2023-10-22 Cleaning up 3d files
    [218-108.stp, 530480410.stp, 530480510.stp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]
2023-10-22 Removing files
    [218-108.stp, 530480410.stp, 530480510.stp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]
2023-10-22 Continued cleaning things up
    [530480410.stp, 530480510.stp]
2023-10-22 Added new footprint for pyrotechnic channels
2023-10-22 Finished layout with modified pyro terminal blocks
    [2601-1108.stp, Flight Computer.kicad_pcb, pyro-channels.kicad_sch]
2023-10-23 Added different 3d models for terminal blocks
    [Flight Computer.kicad_pcb, pyro-channels.kicad_sch]
2023-10-28 Modified connector footprints
    [Flight Computer.kicad_pcb]
2023-11-13 Match what was sent to JLC
    [Flight Computer.kicad_pcb]

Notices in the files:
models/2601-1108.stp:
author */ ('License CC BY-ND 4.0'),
